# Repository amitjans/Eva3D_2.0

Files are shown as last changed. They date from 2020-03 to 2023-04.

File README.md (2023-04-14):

# Assembly Manual: Eva 4.0
<p align="center">
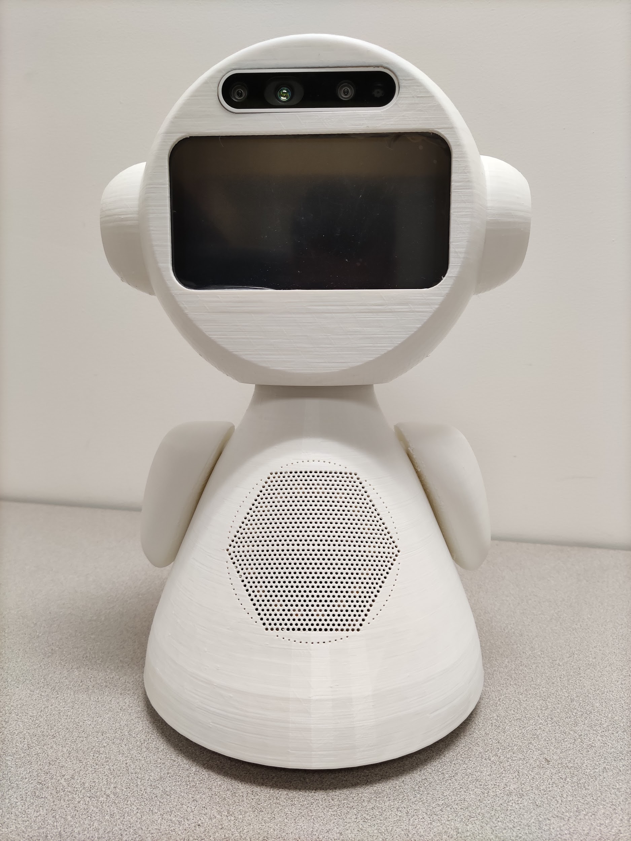
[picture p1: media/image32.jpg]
    
</p>

# Versions of the social robot Eva

Three versions of the social robot Eva were designed. The assembly demonstrated, as well as the images used in this manual, correspond to the most equipped version of the robot.

| Nombre | foto | Descripción |
| :--- | :---: | :--- |
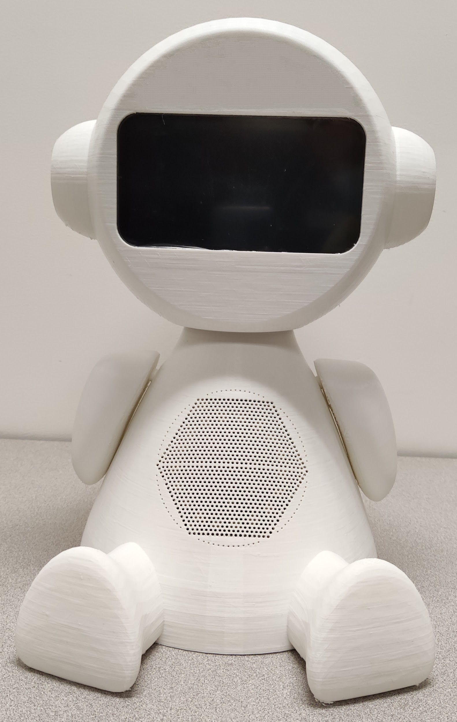
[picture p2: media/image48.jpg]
| Basic Eva |  | The basic version of the social robot Eva has three capabilities: <ul><li>Verbal interaction: through an array of microphones (Matrix Voice) and a speaker.</li><li>Eyes: through a 5.5” screen.</li><li>Head movement: through the use of two motors (Dynamixel AX-12A (Hard#10)).</li></ul> |
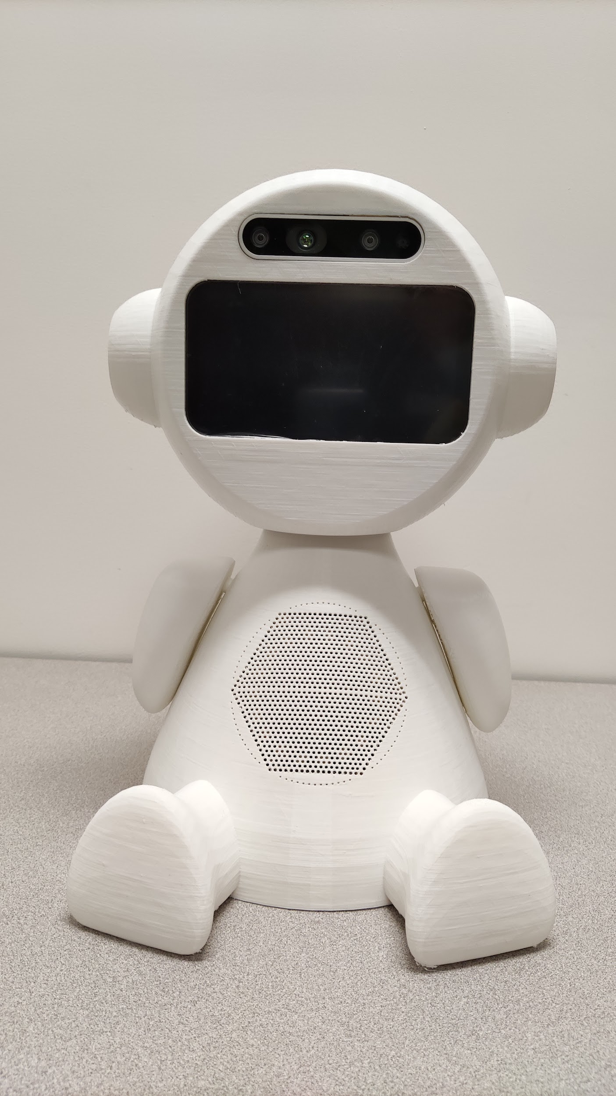
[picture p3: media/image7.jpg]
| Eva with camera |  | The camera version of the Eva social robot inherits the capabilities of the basic version. The new capabilities of this version are: <ul><li>Vision: using an Intel RealSense Depth Camera D435i (Hard#4).</li></ul> |
| Eva with camera and movement |  | The camera and movement version of the social robot Eva inherits the capabilities of the camera version. The new capabilities of this version include: <ul><li>Movement: using two new motors and wheels.</li></ul> |

# Basic Eva

<table border="0">
 <tr>
    <td>
        <ul>
            <li>Components
                <ul>
                    <li>Printables
                        <ul>
                            <li><a href="#Imp#1">Imp#1</a></li>
                            <li><a href="#Imp#3">Imp#3</a></li>
                            <li><a href="#Imp#5">Imp#5</a></li>
                            <li><a href="#Imp#7">Imp#7</a></li>
                            <li><a href="#Imp#9">Imp#9</a></li>
                            <li><a href="#Imp#10">Imp#10</a></li>
                            <li><a href="#Imp#11">Imp#11</a></li>
                            <li><a href="#Imp#12">Imp#12</a></li>
                            <li><a href="#Imp#13">Imp#13</a></li>
                            <li><a href="#Imp#14">Imp#14</a></li>
                        </ul>
                    </li>
                </ul>
                <ul>
                    <li>Electronics
                        <ul>
                            <li><a href="#Hard#1">Hard#1</a></li>
                            <li><a href="#Hard#2">Hard#2</a></li>
                            <li><a href="#Hard#17">Hard#17</a></li>
                            <li><a href="#Hard#8">Hard#8</a></li>
                            <li><a href="#Hard#10">Hard#10</a></li>
                            <li><a href="#Hard#11">Hard#11</a></li>
                            <li><a href="#Hard#13">Hard#13</a></li>
                            <li><a href="#Hard#14">Hard#14</a></li>
                            <li><a href="#Hard#15">Hard#15</a></li>
                        </ul>
                    </li>
                </ul>
            </li>
        </ul>
    </td>
    <td>
        <ul>
            <li>Assembly
                <ul>
                    <li><a href="#armando-el-cuello">Assembling the neck</a>
                        <ul>
                            <li><a href="#versión-estática">Static Version</a></li>
                            <li><a href="#raspberry-y-matrix-voice">Raspberry and Matrix Voice</a></li>
                        </ul>
                    </li>
                    <li><a href="#base-del-robot">Robot Base</a>
                        <ul>
                            <li><a href="#estático">Static</a></li>
                        </ul>
                    </li>
                    <li><a href="#ensamblaje-del-interior">Assembly of the interior</a></li>
                    <li><a href="#ensamblaje-de-la-cabeza">Assembly of the head</a>
                        <ul>
                            <li><a href="#sin-cámara">Without camera</a></li>
                            <li><a href="#pantalla">Display</a></li>
                        </ul>
                    </li>
                    <li><a href="#ensamblaje-final">Final assembly</a></li>
                </ul>
            </li>
        </ul>
    </td>
    <td></td>
 </tr>
</table>

# Eva with camera

<table border="0">
 <tr>
    <td>
        <ul>
            <li>Components
                <ul>
                    <li>Printables
                        <ul>
                            <li><a href="#Imp#2">Imp#2</a></li>
                            <li><a href="#Imp#3">Imp#3</a></li>
                            <li><a href="#Imp#4">Imp#4</a></li>
                            <li><a href="#Imp#5">Imp#5</a></li>
                            <li><a href="#Imp#7">Imp#7</a></li>
                            <li><a href="#Imp#9">Imp#9</a></li>
                            <li><a href="#Imp#10">Imp#10</a></li>
                            <li><a href="#Imp#11">Imp#11</a></li>
                            <li><a href="#Imp#12">Imp#12</a></li>
                            <li><a href="#Imp#13">Imp#13</a></li>
                            <li><a href="#Imp#14">Imp#14</a></li>
                        </ul>
                    </li>
                </ul>
                <ul>
                    <li>Electronics
                        <ul>
                            <li><a href="#Hard#1">Hard#1</a></li>
                            <li><a href="#Hard#2">Hard#2</a></li>
                            <li><a href="#Hard#17">Hard#17</a></li>
                            <li><a href="#Hard#4">Hard#4</a></li>
                            <li><a href="#Hard#8">Hard#8</a></li>
                            <li><a href="#Hard#10">Hard#10</a></li>
                            <li><a href="#Hard#11">Hard#11</a></li>
                            <li><a href="#Hard#13">Hard#13</a></li>
                            <li><a href="#Hard#14">Hard#14</a></li>
                            <li><a href="#Hard#15">Hard#15</a></li>
                        </ul>
                    </li>
                </ul>
            </li>
        </ul>
    </td>
    <td>
        <ul>
            <li>Assembly
                <ul>
                    <li><a href="#armando-el-cuello">Assembling the neck</a>
                        <ul>
                            <li><a href="#versión-estática">Static Version</a></li>
                            <li><a href="#raspberry-y-matrix-voice">Raspberry and Matrix Voice</a></li>
                        </ul>
                    </li>
                    <li><a href="#base-del-robot">Robot Base</a>
                        <ul>
                            <li><a href="#estático">Static</a></li>
                        </ul>
                    </li>
                    <li><a href="#ensamblaje-del-interior">Assembly of the interior</a></li>
                    <li><a href="#ensamblaje-de-la-cabeza">Assembly of the head</a>
                        <ul>
                            <li><a href="#con-cámara">With camera</a>
                                <ul>
                                    <li><a href="#cámara">Camera</a></li>
                                </ul>
                            </li>
                            <li><a href="#pantalla">Display</a></li>
                        </ul>
                    </li>
                    <li><a href="#ensamblaje-final">Final assembly</a></li>
                </ul>
            </li>
        </ul>
    </td>
    <td></td>
 </tr>
</table>

# Eva with camera and movement

<table border="0">
 <tr>
    <td>
        <ul>
            <li>Components
                <ul>
                    <li>Printables
                        <ul>
                            <li><a href="#Imp#2">Imp#2</a></li>
                            <li><a href="#Imp#3">Imp#3</a></li>
                            <li><a href="#Imp#6">Imp#4</a></li>
                            <li><a href="#Imp#8">Imp#5</a></li>
                            <li><a href="#Imp#9">Imp#7</a></li>
                            <li><a href="#Imp#10">Imp#9</a></li>
                            <li><a href="#Imp#11">Imp#10</a></li>
                            <li><a href="#Imp#12">Imp#11</a></li>
                            <li><a href="#Imp#13">Imp#12</a></li>
                            <li><a href="#Imp#14">Imp#13</a></li>
                        </ul>
                    </li>
                </ul>
                <ul>
                    <li>Electronics
                        <ul>
                            <li><a href="#Hard#1">Hard#1</a></li>
                            <li><a href="#Hard#2">Hard#2</a></li>
                            <li><a href="#Hard#3">Hard#3</a></li>
                            <li><a href="#Hard#4">Hard#4</a></li>
                            <li><a href="#Hard#5">Hard#5</a></li>
                            <li><a href="#Hard#6">Hard#6</a></li>
                            <li><a href="#Hard#7">Hard#7</a></li>
                            <li><a href="#Hard#8">Hard#8</a></li>
                            <li><a href="#Hard#9">Hard#9</a></li>
                            <li><a href="#Hard#10">Hard#10</a></li>
                            <li><a href="#Hard#11">Hard#11</a></li>
                            <li><a href="#Hard#12">Hard#12</a></li>
                            <li><a href="#Hard#13">Hard#13</a></li>
                            <li><a href="#Hard#14">Hard#14</a></li>
                            <li><a href="#Hard#15">Hard#15</a></li>
                        </ul>
                    </li>
                </ul>
            </li>
        </ul>
    </td>
    <td>
        <ul>
            <li>Assembly
                <ul>
                    <li><a href="#armando-el-cuello">Assembling the neck</a>
                        <ul>
                            <li><a href="#versión-móvil">Mobile Version</a></li>
                            <li><a href="#raspberry-y-matrix-voice">Raspberry and Matrix Voice</a></li>
                        </ul>
                    </li>
                    <li><a href="#base-del-robot">Robot Base</a>
                        <ul>
                            <li><a href="#móvil">Mobile</a></li>
                        </ul>
                    </li>
                    <li><a href="#ensamblaje-del-interior">Assembly of the interior</a></li>
                    <li><a href="#ensamblaje-de-la-cabeza">Assembly of the head</a>
                        <ul>
                            <li><a href="#con-cámara">With camera</a>
                                <ul>
                                    <li><a href="#cámara">Camera</a></li>
                                </ul>
                            </li>
                            <li><a href="#pantalla">Display</a></li>
                        </ul>
                    </li>
                    <li><a href="#ensamblaje-final">Final assembly</a></li>
                </ul>
            </li>
        </ul>
    </td>
    <td></td>
 </tr>
</table>

# Assembling the neck

To begin the assembly of the Eva robot, we will start with the interior, specifically the section that allows the head to move. For this, we will need the Dynamixel AX-12A (Hard#10) motors as well as the screws and parts included by the manufacturers along with these motors ([Hard#8](#Hard#8) and [#Hard#11](Hard#11)). The sequence of steps is shown below.

<table>
<tr>
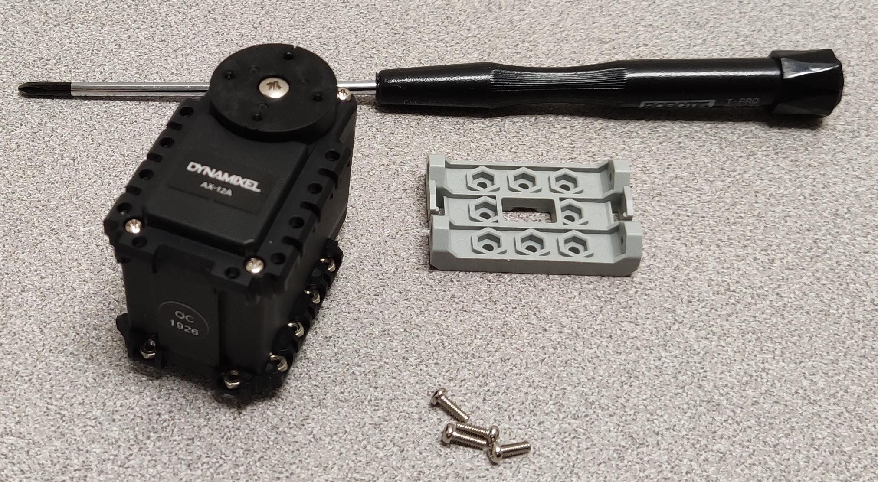
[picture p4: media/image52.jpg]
<td></td>
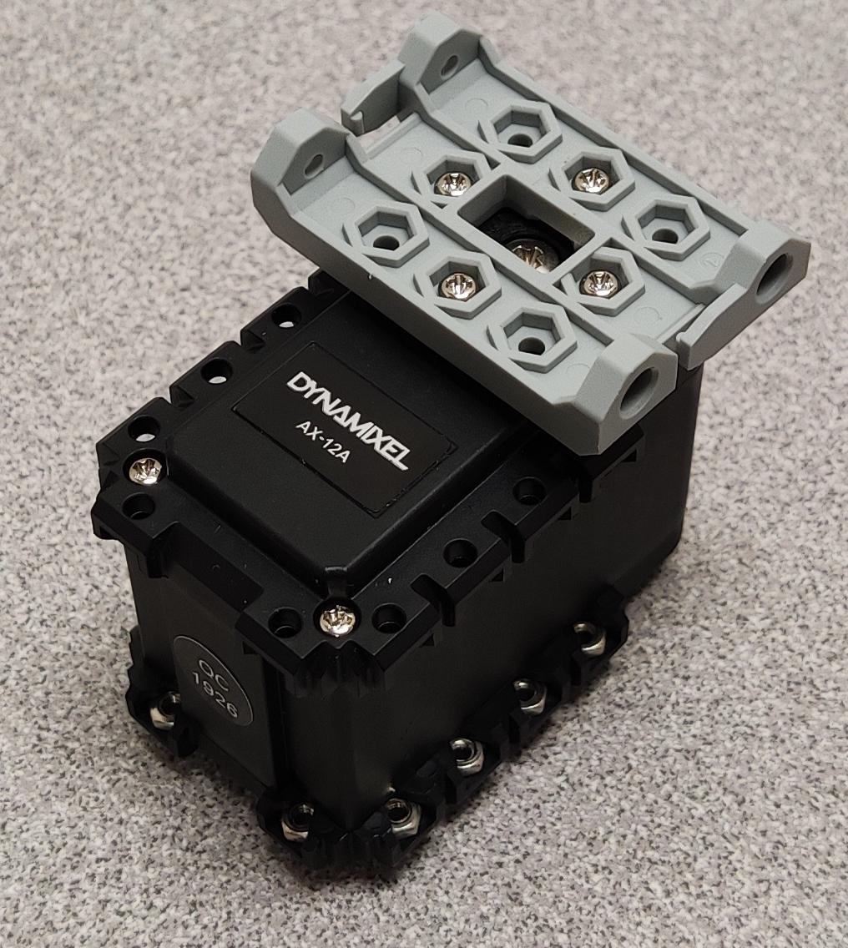
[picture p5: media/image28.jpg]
<td></td>
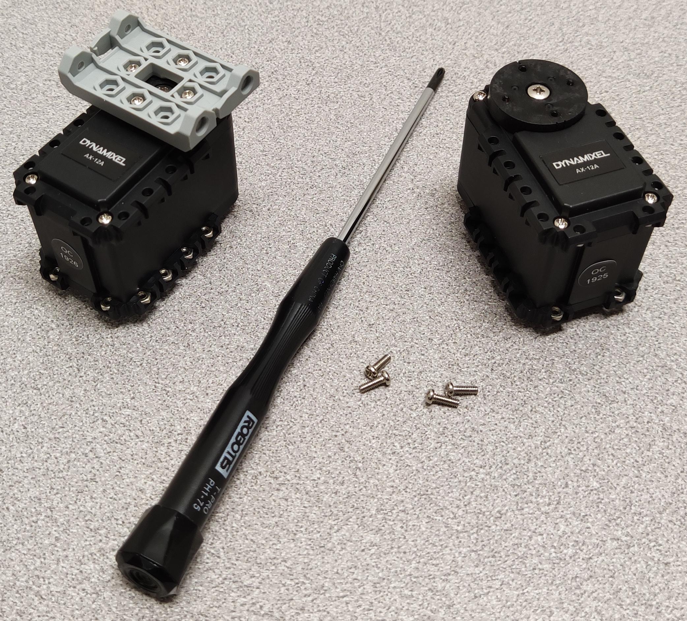
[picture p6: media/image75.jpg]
<td></td>
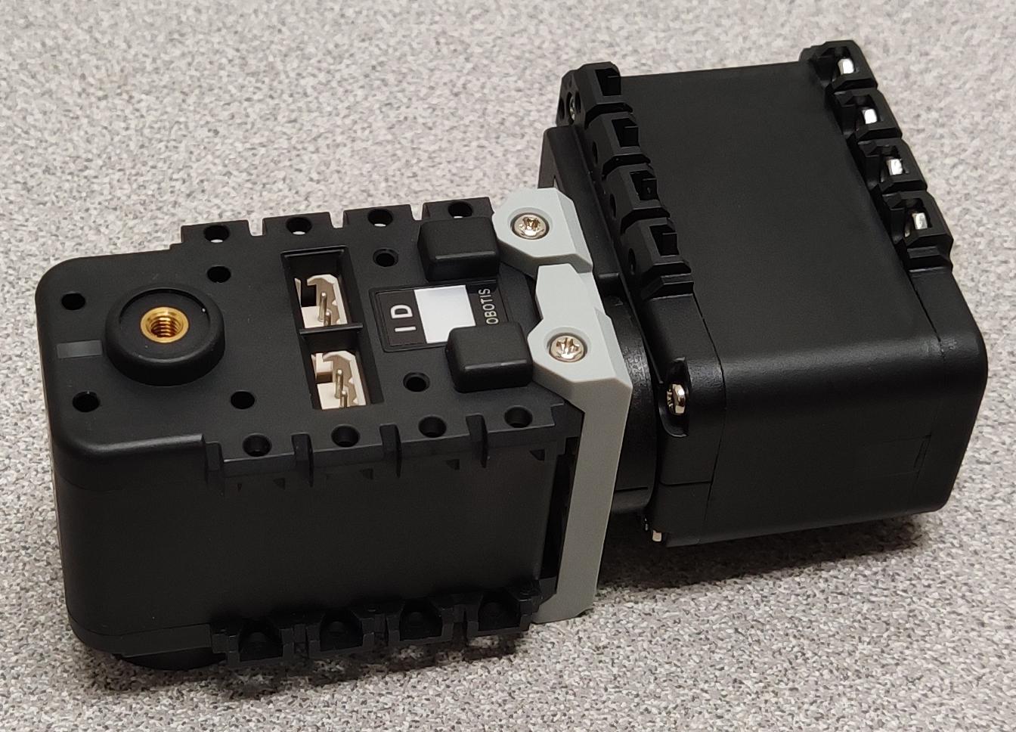
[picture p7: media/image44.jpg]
<td></td>
</tr>
<tr>
<td colspan="2">Attach the base motor (Hard#10) to the Bioloid Frame F3 (Hard#11).</td>
<td colspan="2">Attach the second motor (Hard#10) to the first using the Bioloid Frame F3 (Hard#11).</td>
</tr>
<tr>
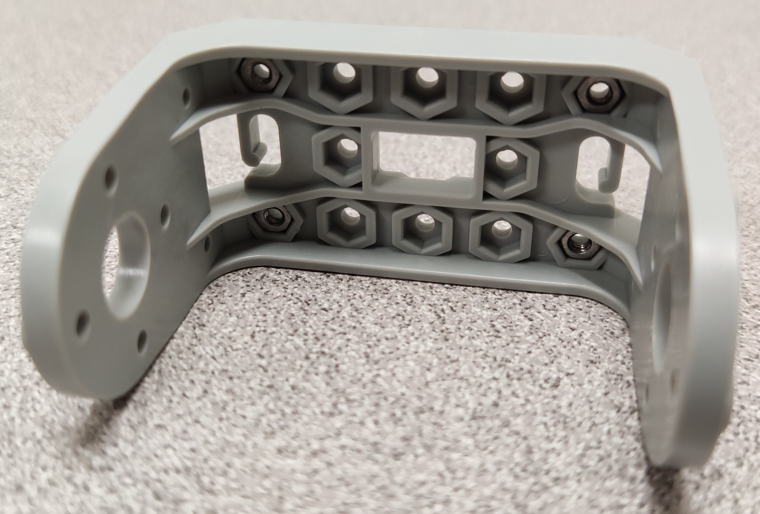
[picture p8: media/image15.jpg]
<td colspan="2"></td>
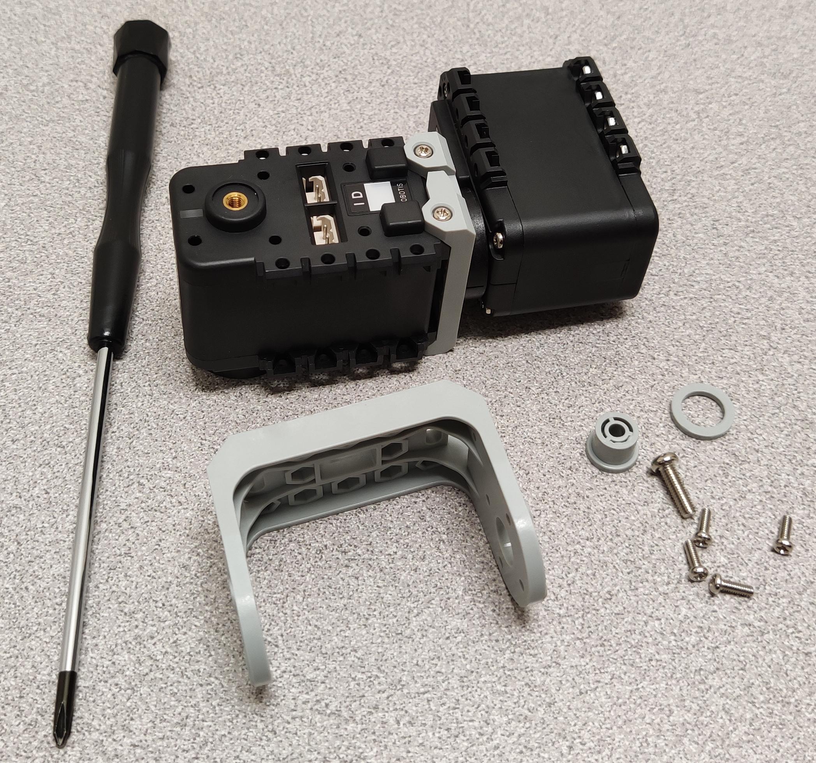
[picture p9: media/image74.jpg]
<td></td>
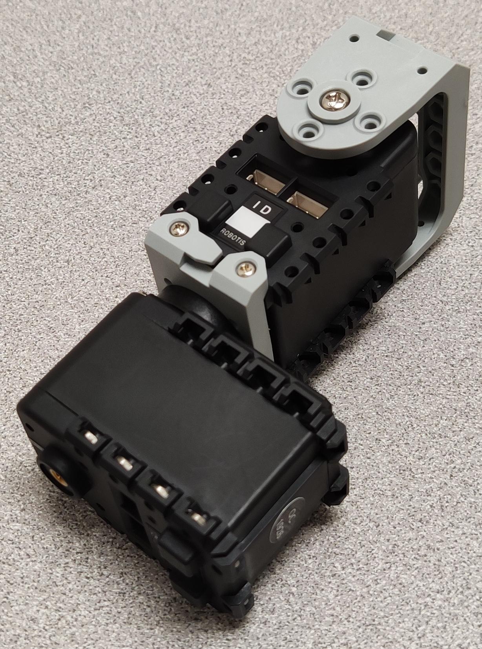
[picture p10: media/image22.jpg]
<td></td>
</tr>
<tr>
<td colspan="2">Place M2 nuts on the head support, Bioloid Frame F2 (Hard#8).</td>
<td colspan="2">Attach the head support, Bioloid Frame F2 (Hard#8) to the second motor (Hard#10).</td>
</tr>
</table>

Once both motors are attached, the first one will be screwed onto the "Motor Base". For this, we will use the screws provided by the seller. The nuts will be fixed to the motor and the screws will come from the opposite side of the motors.

<table>
<tr>
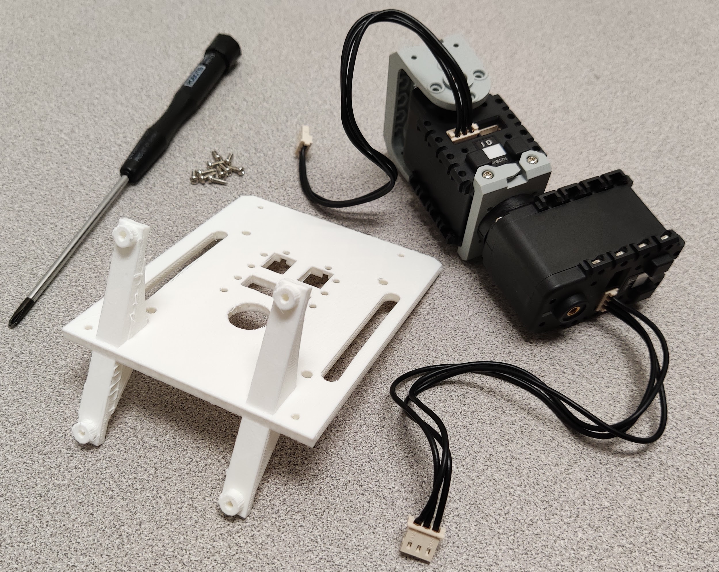
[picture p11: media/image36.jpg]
<td></td>
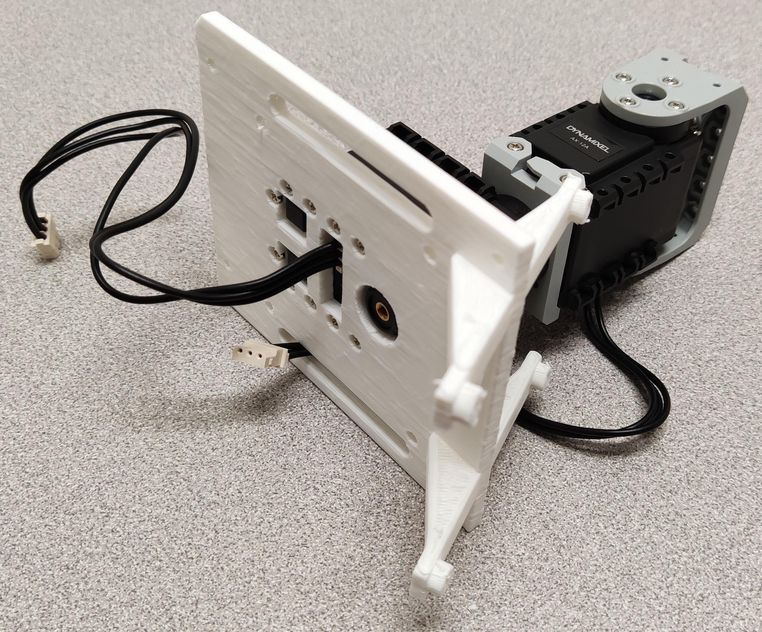
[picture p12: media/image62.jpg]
<td></td>
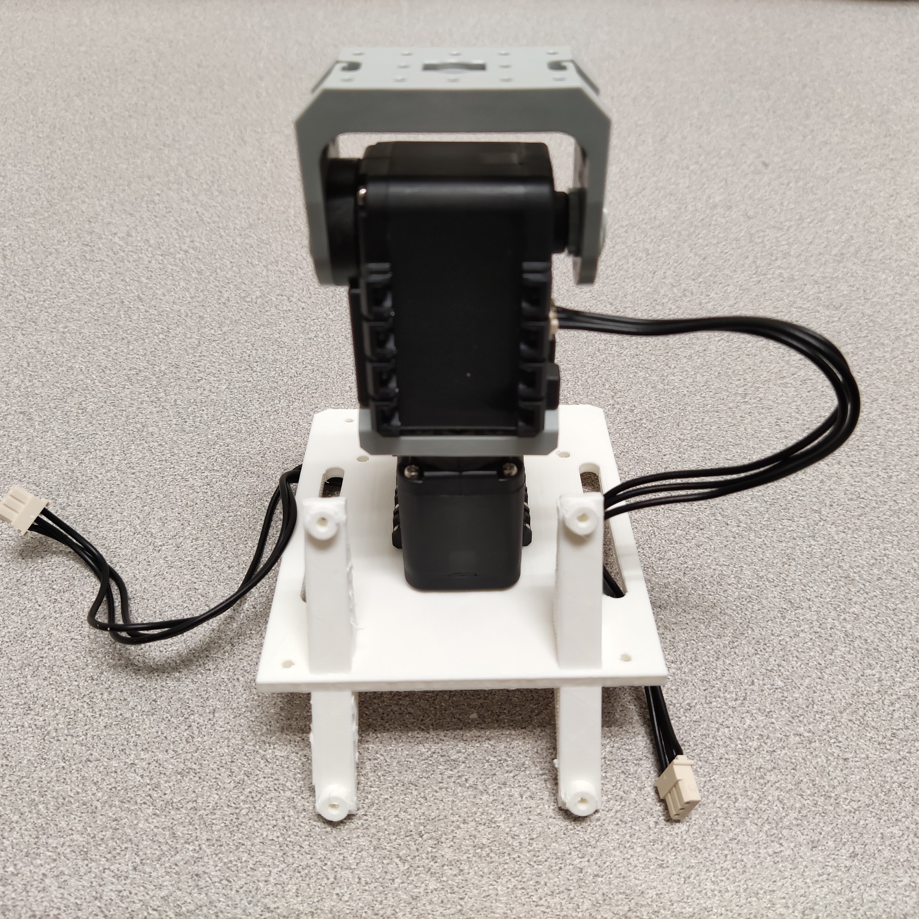
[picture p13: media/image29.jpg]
<td></td>
</tr>
<tr>
<td colspan="3">Fix the motor assembly (Hard#10) to the Motor Base (Imp#9)</td>
</tr>
</table>

**Note:** Before continuing with the next step, it is recommended to connect the cables that will communicate the motors with the control board to the motors.

## Static version 

Next, we will attach the control board responsible for the motors to the "Motor Base" (Imp#9Imp#9). In this case, we have chosen the "ArbotiX-M" (Hard#17Hard#17) control board. We will use four "PCB Mounts" (Imp#15Imp#15) to attach the board to the "Motor Base" (Imp#9Imp#9), using M3x8 screws for both.

## Mobile version

Afterwards, we will attach the motor control board, in this case, the OpenCR 1.0 (Hard#3), to the “base for motors” (Imp#9) using four "PCB Mounts" (Imp#14). The mounts will be screwed into the “base for motors” (Imp#9) and the controller board will be attached to these mounts using M2.5x8 screws and M2.5 nuts.

<table>
<tr>
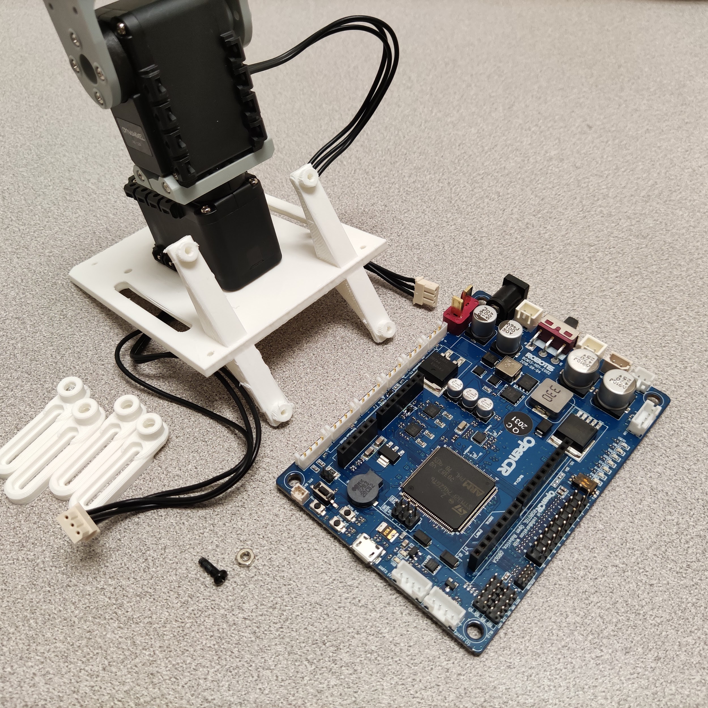
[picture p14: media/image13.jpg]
<td colspan="2"></td>
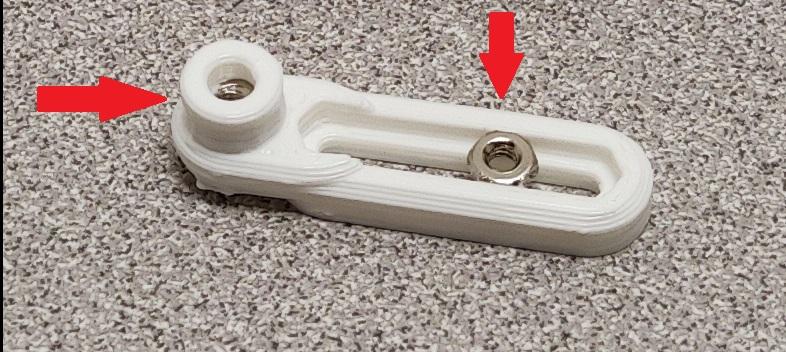
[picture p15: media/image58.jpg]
<td colspan="2"></td>
</tr>
<tr>
<td colspan="4">Next, we will mount the OpenCR 1.0 board (Hard#3) onto the motor base (Imp#9) using four PCB supports (Imp#14). To do this, we will initially place 2 M2.5 nuts on each PCB support (Imp#14) as shown in the image above.</td>
</tr>
<tr>
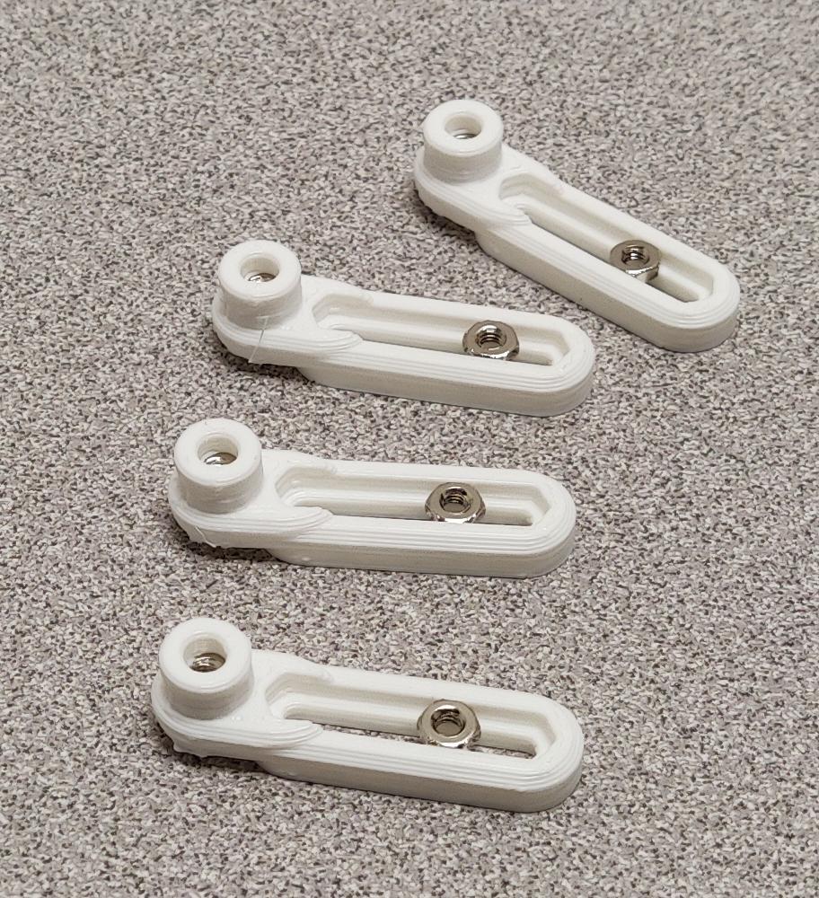
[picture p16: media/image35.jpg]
<td></td>
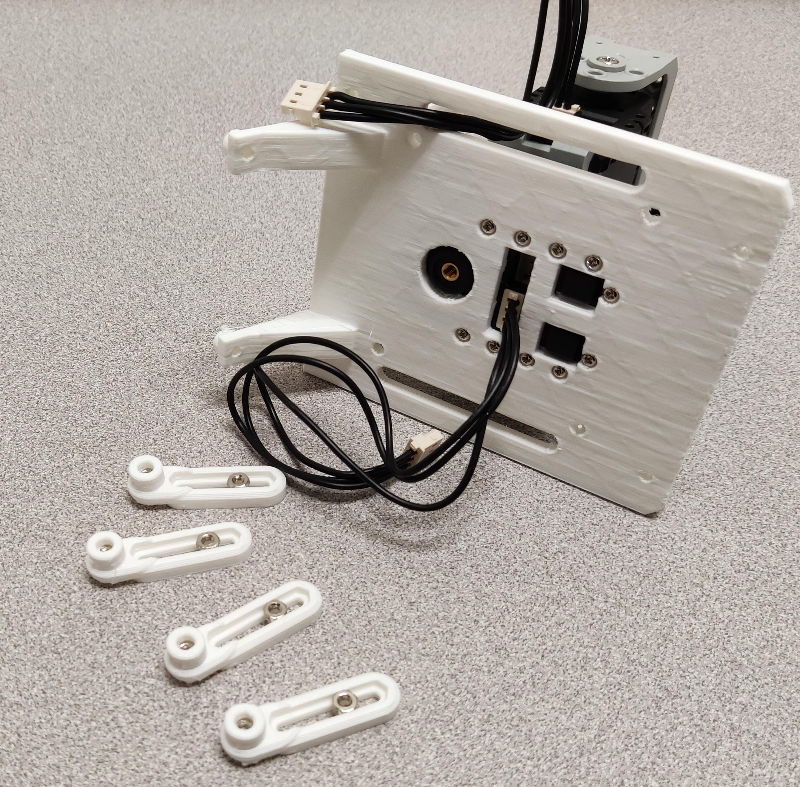
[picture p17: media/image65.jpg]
<td></td>
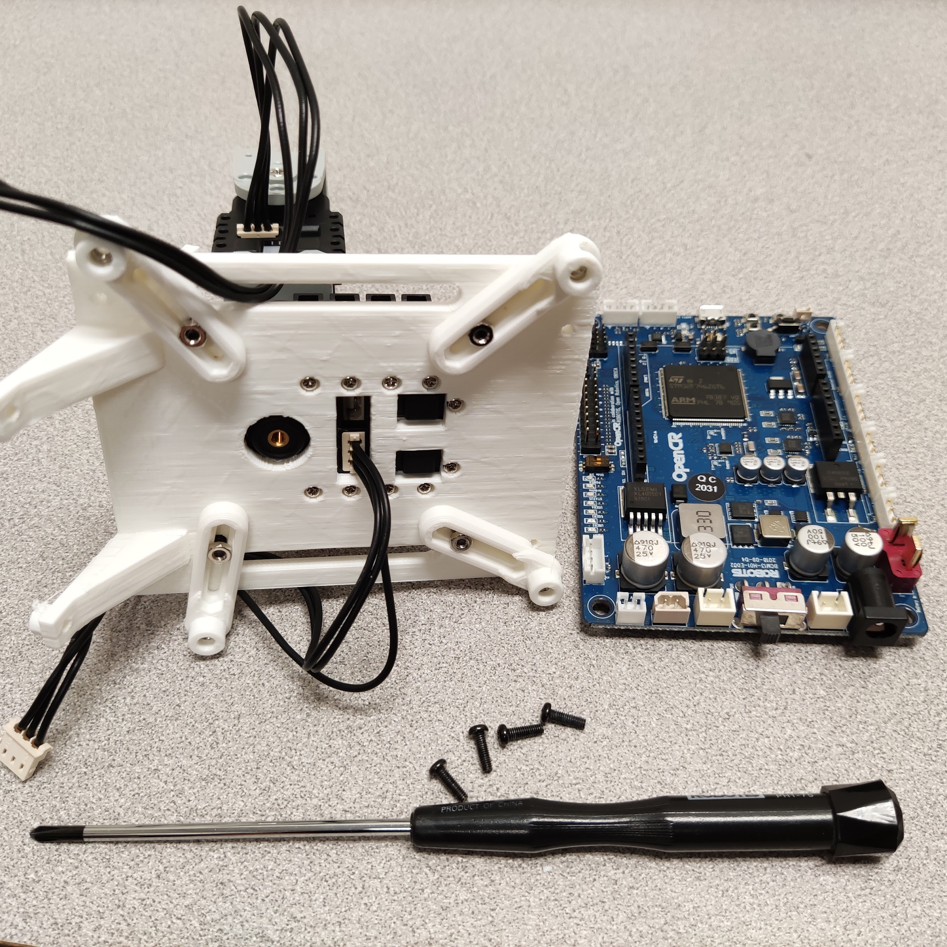
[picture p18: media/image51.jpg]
<td></td>
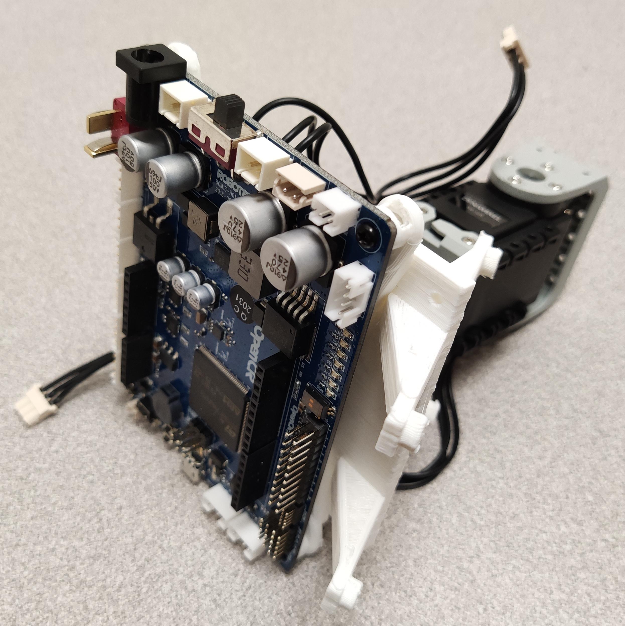
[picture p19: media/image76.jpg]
<td></td>
</tr>
<tr>
<td colspan="4">Finally, we screw the PCB supports (Imp#14) and the OpenCR 1.0 board (Hard#3) to them onto the motor base (Imp#9).</td>
</tr>
</table>

## Raspberry and Matrix Voice

Once the previous step is completed, the Raspberry Pi (Hard#13) and the Matrix Voice (Hard#14) can be placed in their positions. The Raspberry Pi (Hard#13) will be secured to the base using four M2.5x12 screws.

<table>
<tr>
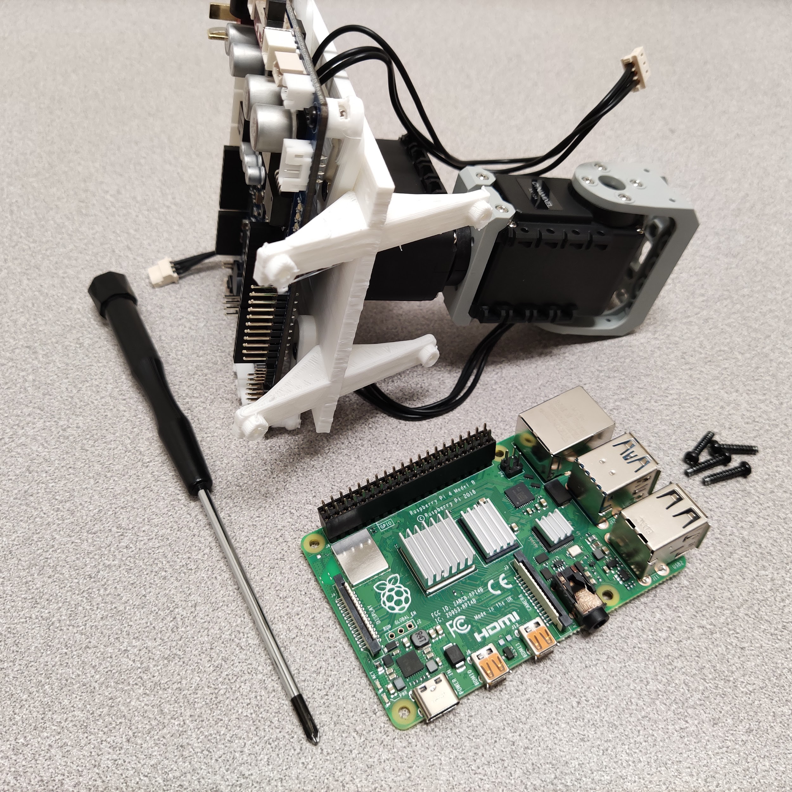
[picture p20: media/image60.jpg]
<td></td>
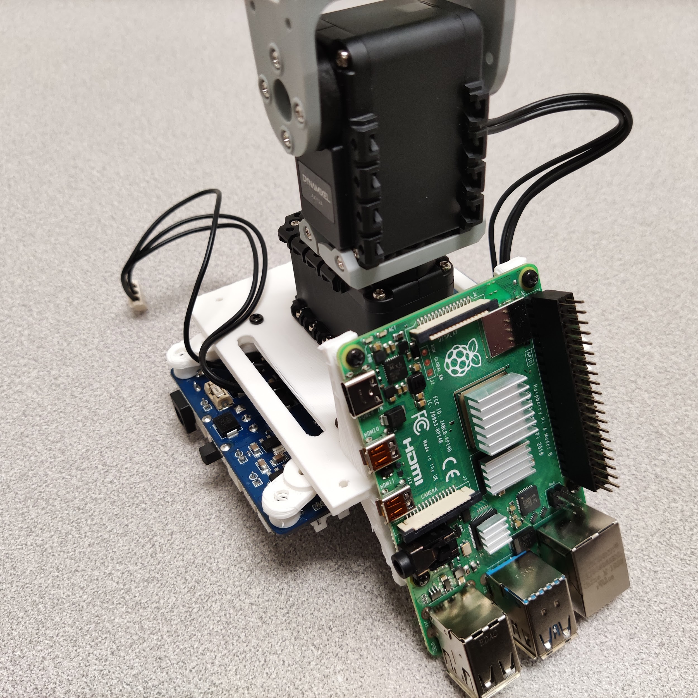
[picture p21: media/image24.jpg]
<td></td>
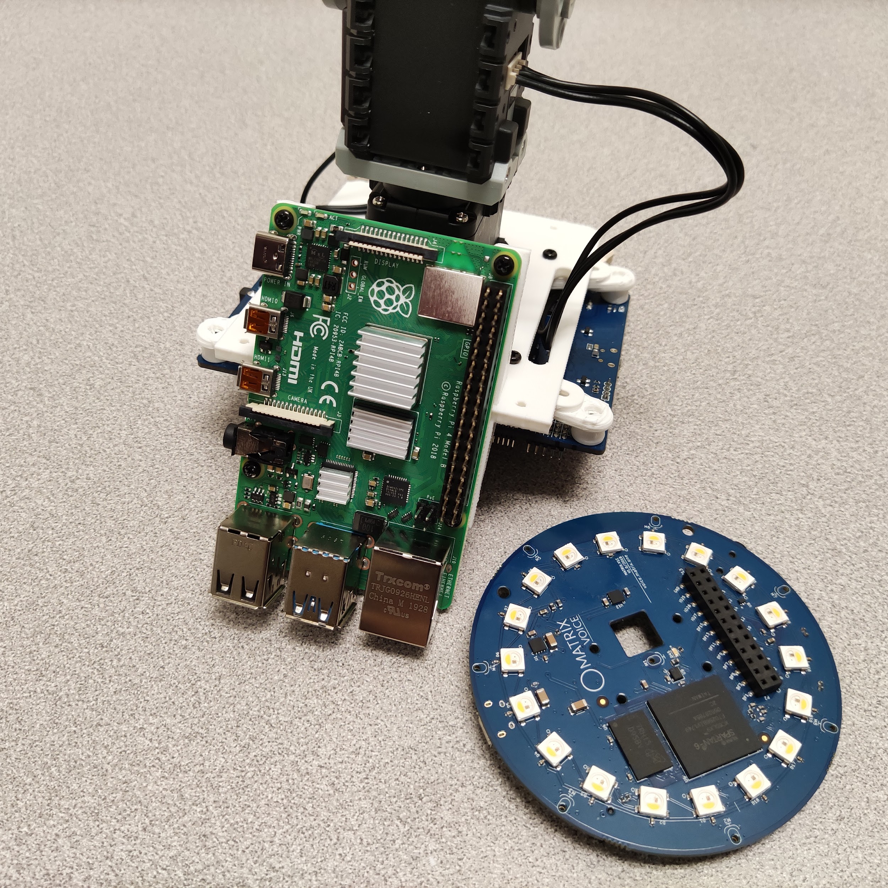
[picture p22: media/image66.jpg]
<td></td>
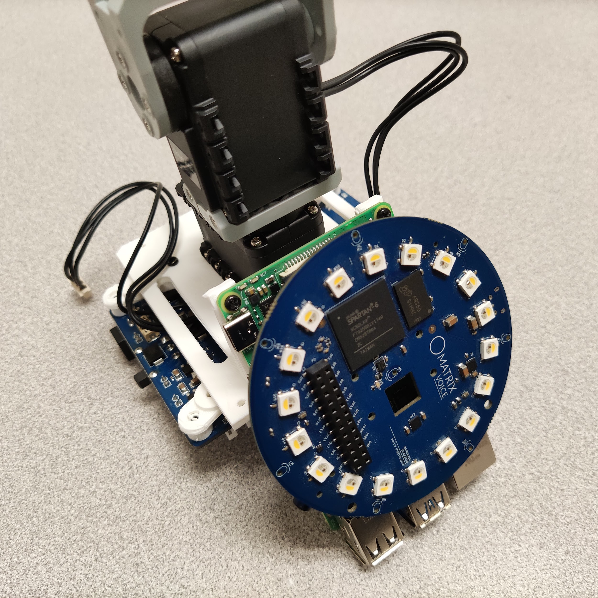
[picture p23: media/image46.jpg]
<td></td>
</tr>
<tr>
<td colspan="2">Placing the Raspberry Pi (Hard#13) on the motor base (Imp#9).</td>
<td colspan="2">Placing the Matrix Voice (Hard#14) on top of the Raspberry Pi (Hard#13) using a GPIO Stacking Header (Hard#15).</td>
</tr>
</table>

# Base of the Robot

The assembly of the robot base will depend on the version of the robot being assembled: static or mobile.

## Static

For the static version of the robot, we will use the Base (Imp#7) to which we will attach the battery (LI-PO 11.1V 1800mAh Lb-12 19.98Wh 5C) (Hard#5) with the structures that protrude from the center of the base.

## Mobile

For this step, we will need two XL430-W250-T motors (Hard#9), two wheels (Hard#6), and two tires (Hard#7), a lithium battery - for this case, the "LI-PO 11.1V 1800mAh Lb-12c 19.98Wh 5C" (Hard#5) was used, a ball caster (Hard#12), and the "Mobile Base" (Imp#8) to which everything will be attached.

First, the tires (Hard#7) will be placed on the wheels (Hard#6), and then the wheels will be screwed onto the motors (Hard#9) using four M2x4 screws for each one.

<table>
<tr>
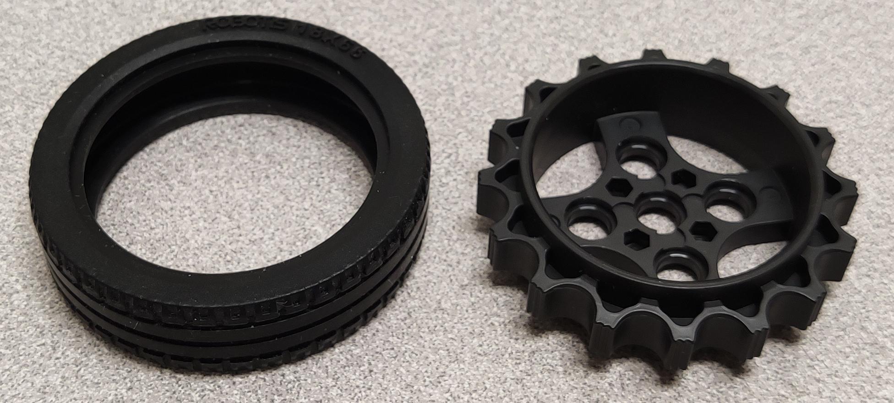
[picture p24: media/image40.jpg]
<td></td>
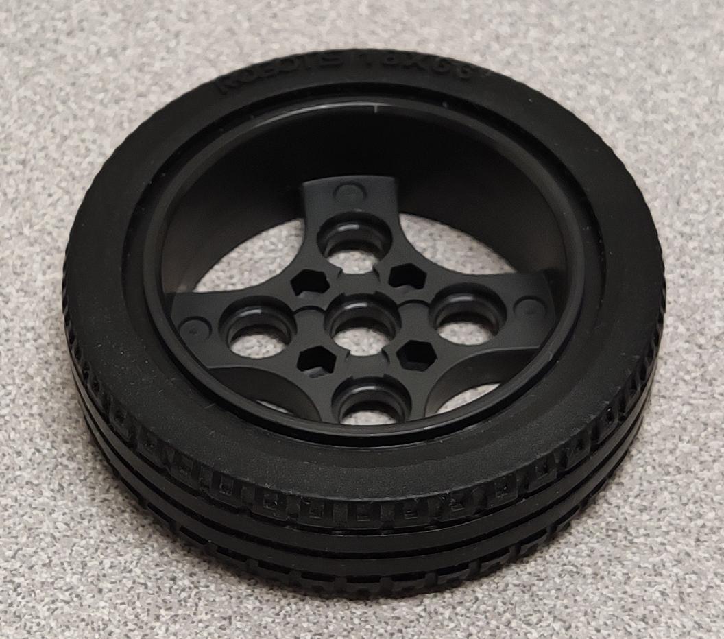
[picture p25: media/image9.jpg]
<td></td>
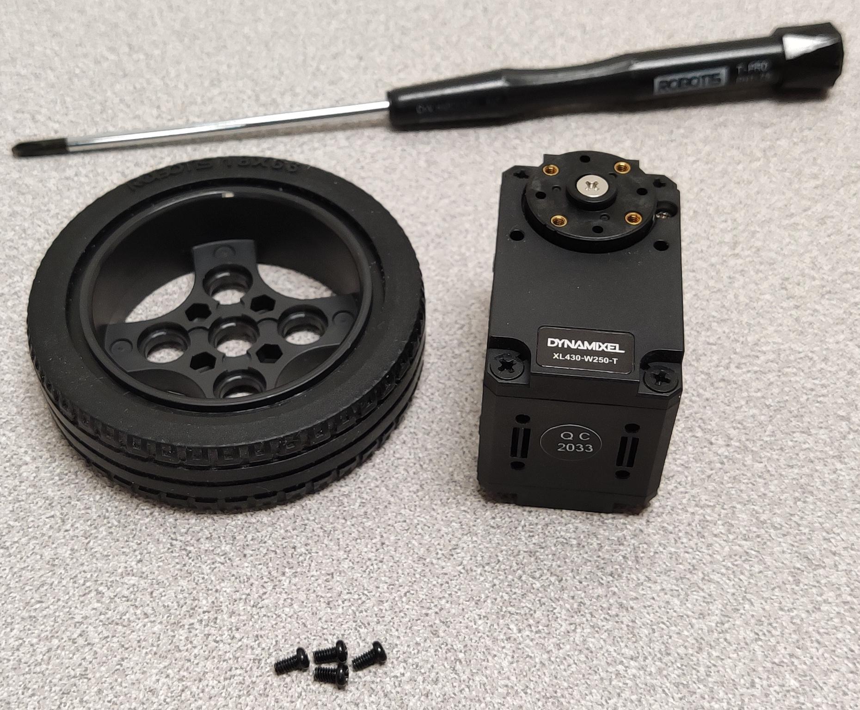
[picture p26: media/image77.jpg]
<td></td>
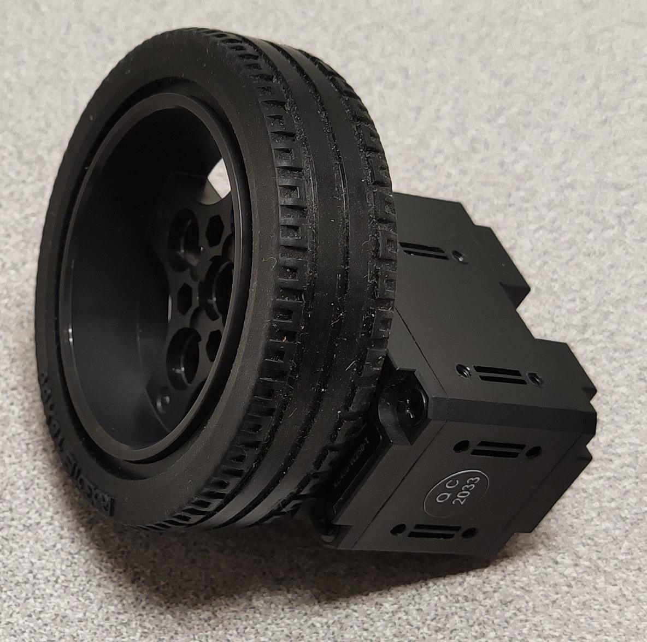
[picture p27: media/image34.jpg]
<td></td>
</tr>
<tr>
<td colspan="4">Assembling the wheels: The tires (Hard#7) will be placed on the wheels (Hard#6) and the latter will be fixed to the motors (Hard#9).</td>
</tr>
</table>

The motors (Hard#9) will be screwed onto the base using four M2.5x12 screws, and for the "Ball Caster" (Hard#12) four M2x6 screws will be used.

<table>
<tr>
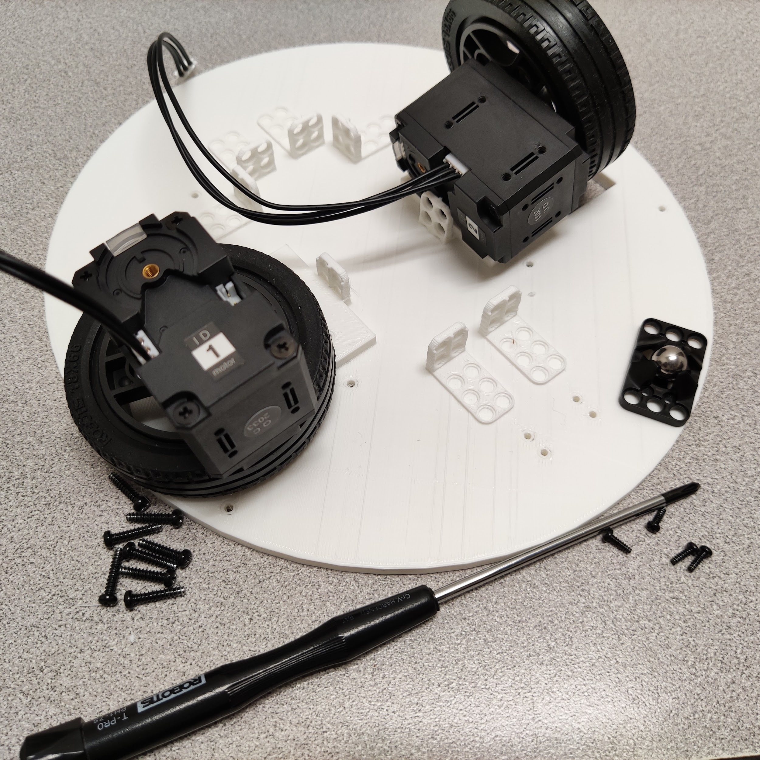
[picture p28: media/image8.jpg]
<td></td>
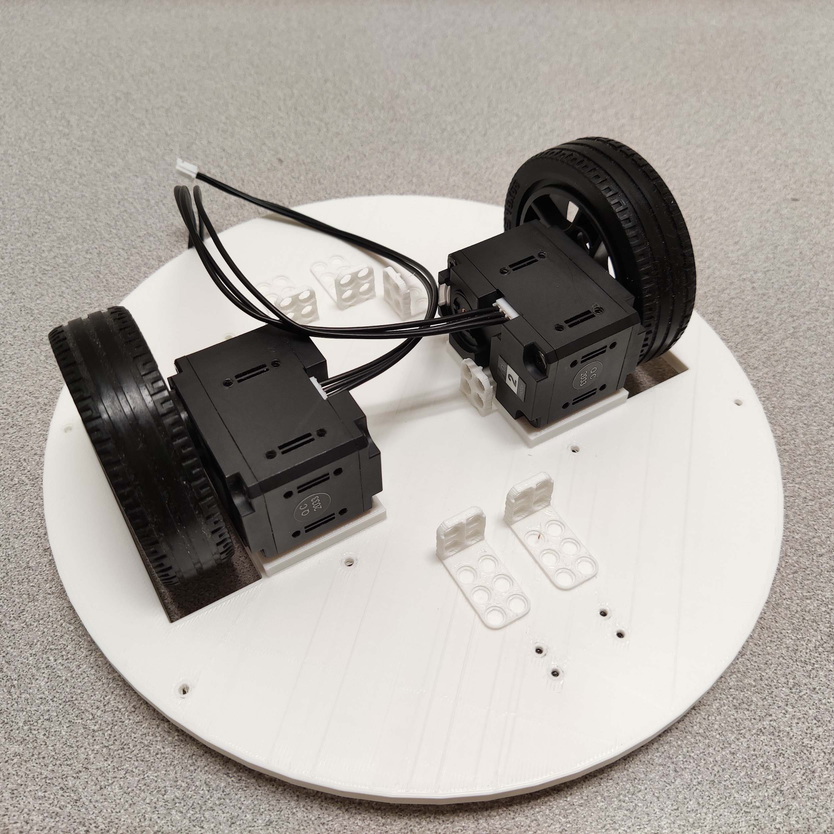
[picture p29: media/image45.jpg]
<td></td>
</tr>
<tr>
<td colspan="2">Assembling the wheels: The tires (Hard#7) will be placed on the wheels (Hard#6) and the latter will be fixed to the motors (Hard#9).</td>
</tr>
</table>

Attaching the previously assembled wheels to the base (Imp#8).

The battery will be attached with the structures that protrude from the center of the base.

# Assembly of the interior

Once the previous two steps are completed, the resulting parts will be joined using four plate supports (Imp#10), for which eight M3x8 screws will be used.

<table>
<tr>
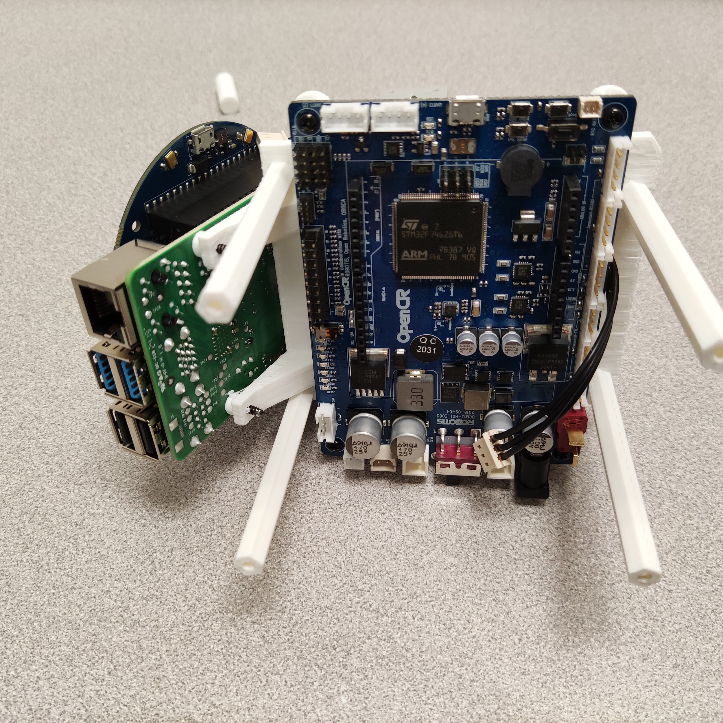
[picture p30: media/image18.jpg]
<td></td>
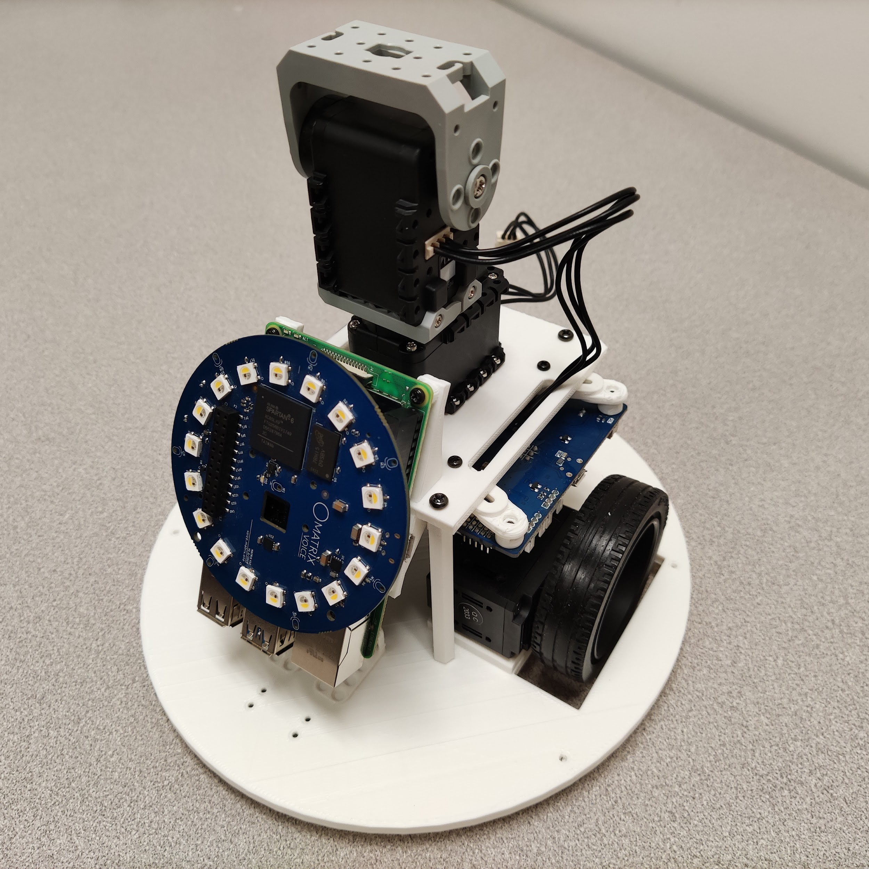
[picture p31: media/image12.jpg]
<td></td>
</tr>
</table>

**Note**: For this case, the shown images correspond to the mobile version of the robot.

**Note**: In the case of the mobile version, it is recommended to connect the motors before joining both parts.

# Assembly of the head

The assembly of the robot's head will depend on the version of the robot being assembled: with camera or without camera.

**Note**: In both cases, this step will vary if a rotating or 90-degree HDMI tip cable is used instead of an adapter, in which case the size of the connector and its orientation must be taken into account.

**Note**: The hole left in the base of the head is intended to allow the cables to pass through. In the assembly carried out, it is taken into account that the HDMI cable, a MicroUSB to USB-A cable (related to the touch functionality of the screen), and the speaker power cable will pass through this space if needed.

## With camera

For this case, we will use the printable parts Head with camera (Imp#2), Back cover of the head (Imp#3), Support for the screen (Imp#13), and Camera spacers (Imp#4), 5.5" screen with a 16:9 aspect ratio (Hard#1), Rotatable male-female HDMI adapter (Hard#2), Intel RealSense Depth Camera D435i (Hard#4), and a Speaker (Hard#16).

### Camera

For this case, the first step will be to place the camera (Hard#4), which will be screwed onto the support designed for it, using two M3x10 screws and two spacers (Imp#4).

<table>
<tr>
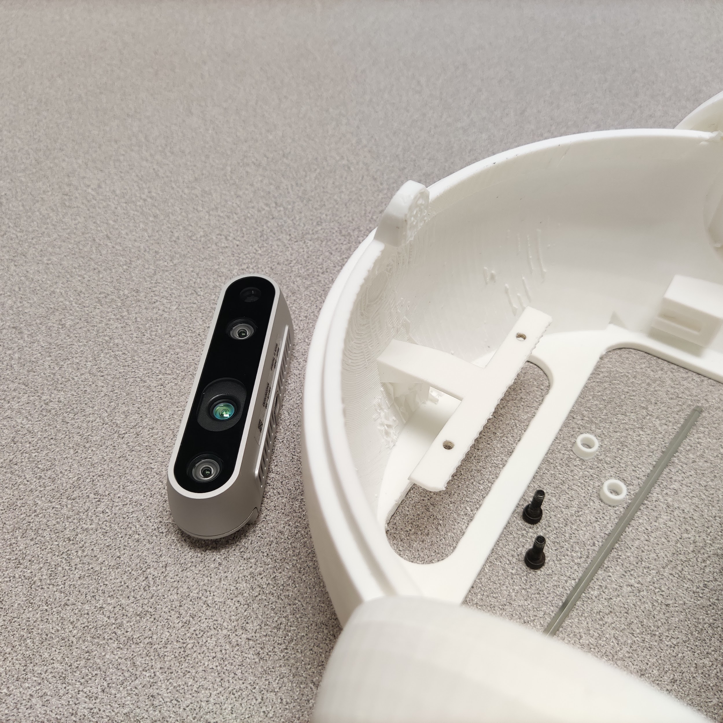
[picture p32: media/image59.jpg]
<td></td>
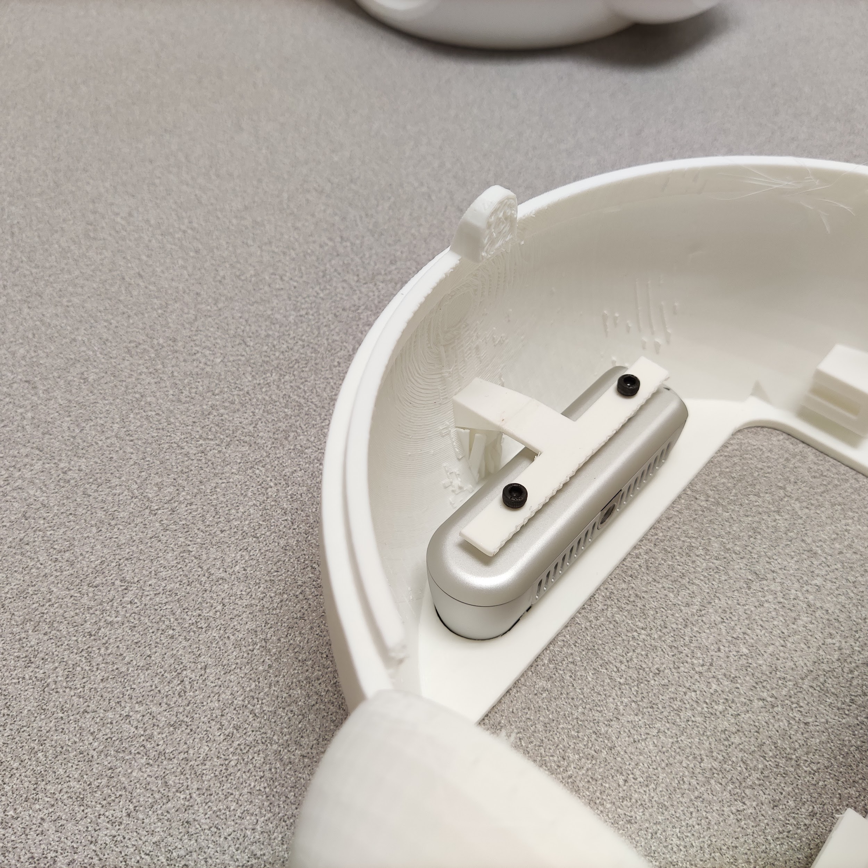
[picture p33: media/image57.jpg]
<td></td>
</tr>
</table>

Next, we will continue with the steps described in the [Screen]() section.

## Without camera

For this case, we will use the printable parts Head (Imp#1), Back cover for the head (Imp#3), and Support for the screen (Imp#13), in addition to a 5.5" screen with a 16:9 aspect ratio (Hard#1), a rotating male-female HDMI adapter (Hard#2), and a Speaker (Hard#16).

## Display

Initially, the screen (Hard#1) will be placed, which is recommended to be connected with the HDMI adapter (Hard#2) and the speaker cable, for greater ease.

<table>
<tr>
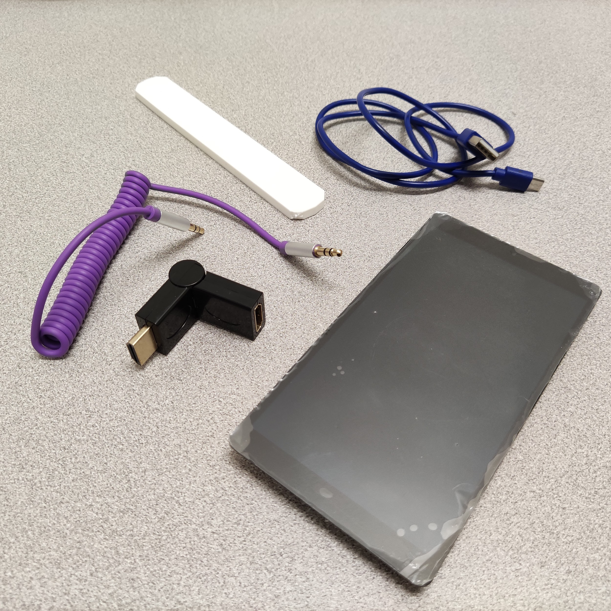
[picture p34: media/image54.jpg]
<td></td>
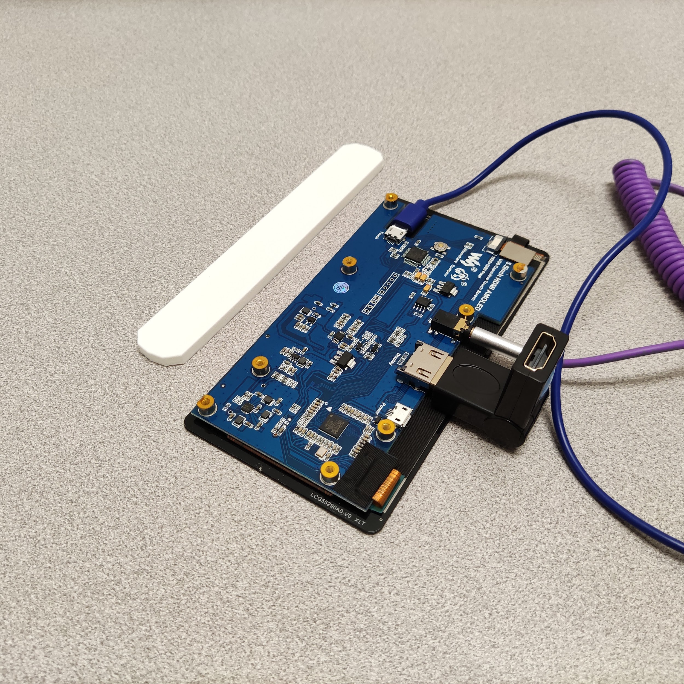
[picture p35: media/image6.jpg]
<td></td>
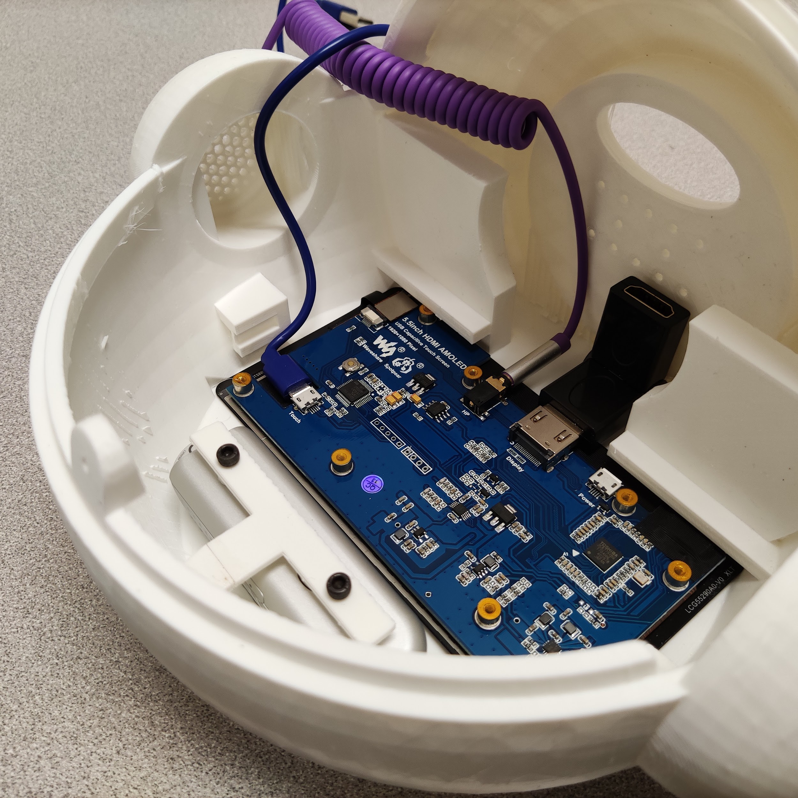
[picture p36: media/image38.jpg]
<td></td>
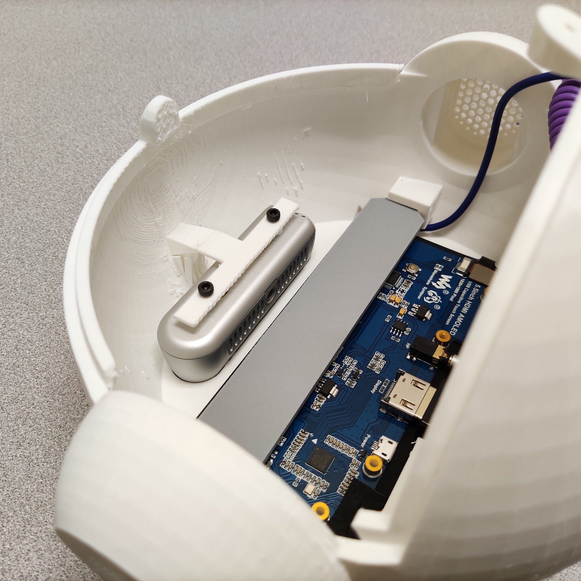
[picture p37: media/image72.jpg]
<td></td>
</tr>
<tr>
<td colspan="2">We connect the cables and the adapter (Hard#2) to the screen (Hard#1).</td>
<td colspan="2">We place the screen (Hard#1) on the head (Imp#1) and fix it with the screen holder (Imp#13).</td>
</tr>
<tr>
    <td colspan="4">
        <p align="center">
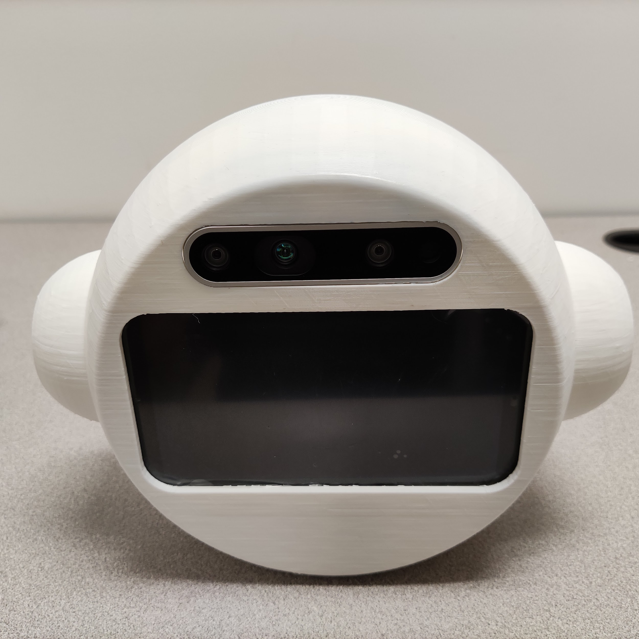
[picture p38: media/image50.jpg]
            </td>
        </p>
    </td>
</tr>
</table>

# Final assembly

To complete the assembly of the robot, we will attach the interior assembly to the body of the robot using four M3x8 screws.

**Note:** There are two versions of the robot body, Static Body (Imp#5) and Mobile Body (Imp#6). The difference between these is the presence/absence of legs. For the mobile version, we will use the version without legs. This choice is a design decision made by our team, as there is no physical element that prevents the use of either variant of the body.

Next, we will attach the Arms (Imp#11) to the body using an Arm Bracket (Imp#12) for each arm.

<p align="center">
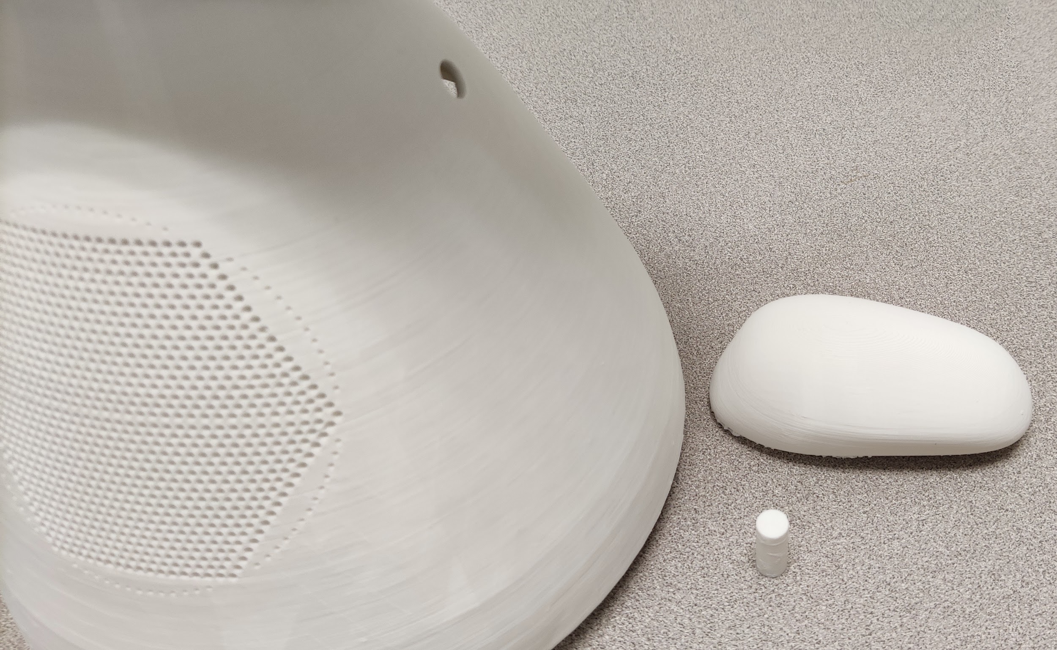
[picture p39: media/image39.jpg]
    
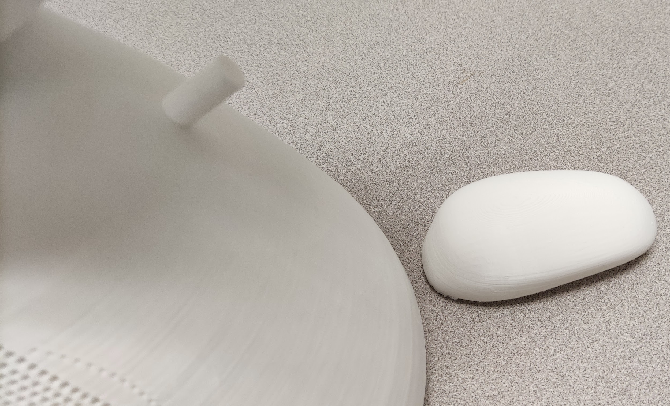
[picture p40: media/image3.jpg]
    
    
</p>

We will place the body (Imp#5 or Imp#6) onto the base (Imp#7 or Imp#8) using four M3x8 screws, so that the body covers the interior and the Matrix Voice is aligned with the body's grille.
Once this step is completed, we will attach the head (Imp#1 or Imp#2), which is screwed onto the neck's "Bioloid Frame F2" (Hard#8), for which we previously placed four nuts.
<p align="center">
    
</p>

For this assembly, a Philips Bluetooth speaker (Hard#16Hard#16) was used, which was fixed to the Head Cover (Imp#3Imp#3) using zip ties.
<p align="center">
    
    
</p>

Finally, we connect the speaker and place the Head Cover (Imp#3Imp#3), which we fix to the head using an M1x8 screw.
<p align="center">
    
    
</p>

Once this step is completed, the robot will look as follows according to the assembled version.

<p align="center">
    
    
    
</p>

# Appendix 1: List of parts

| Nombre | Foto | Descripción |
| :--- | :---: | :--- |
| <span id="Hard#1">Hard#1</span> |  | Waveshare 5.5\" HDMI AMOLED |
| <span id="Hard#2">Hard#2</span> |  | Adaptador HDMI macho-hembra giratorio |
| <span id="Hard#3">Hard#3</span> |  | OpenCR 1.0 |
| <span id="Hard#4">Hard#4</span> |  | Intel® RealSense™ Depth Camera D435i |
| <span id="Hard#5">Hard#5</span> |  | LI-PO 11.1V 1800mAh Lb-12 19.98Wh 5C |
| <span id="Hard#6">Hard#6</span> |  | Rueda x 2 |
| <span id="Hard#7">Hard#7</span> |  | Neumático x 2 |
| <span id="Hard#8">Hard#8</span> |  | Bioloid Frame F2 |
| <span id="Hard#9">Hard#9</span> |  | Dynamixel XL430-W250-T |
| <span id="Hard#10">Hard#10</span> |  | Dynamixel AX-12A |
| <span id="Hard#11">Hard#11</span> |  | Bioloid Frame F3 |
| <span id="Hard#12">Hard#12</span> |  | Ball Caster |
| <span id="Hard#13">Hard#13</span> |  | Raspberry Pi 4 |
| <span id="Hard#14">Hard#14</span> |  | Matrix Voice |
| <span id="Hard#15">Hard#15</span> |  | Cabezal de apilado GPIO |
| <span id="Hard#16">Hard#16</span> |  | Bocina Philips |
| <span id="Hard#17">Hard#17</span> |  | ArbotiX-M |

# Appendix 2: List of printable parts

| Modelo | Nombre | Descarga |
| :--- | :---: | :--- |
| <span id="Imp#1">Imp#1</span> |  | [Cabeza](https://github.com/amitjans/Eva3D_2.0/blob/master/stl/v4/Kit%20basico/cabeza.stl) |
| <span id="Imp#2">Imp#2</span> |  | [Cabeza con cámara](https://github.com/amitjans/Eva3D_2.0/blob/master/stl/v4/Kit%20basico%20%2B%20modulo%20camara/cabeza.stl) |
| <span id="Imp#3">Imp#3</span> |  | [Tapa cabeza](https://github.com/amitjans/Eva3D_2.0/blob/master/stl/v4/Piezas%20generales/tapa_cabeza.stl) |
| <span id="Imp#4">Imp#4</span> |  | [Separadores para la Cámara](https://github.com/amitjans/Eva3D_2.0/blob/master/stl/v4/Kit%20basico%20%2B%20modulo%20camara/separador.stl) 
| <span id="Imp#5">Imp#5</span> |  | [Cuerpo estático](https://github.com/amitjans/Eva3D_2.0/blob/master/stl/v4/Kit%20basico/cuerpo.stl) |  
| <span id="Imp#6">Imp#6</span> |  | [Cuerpo móvil](https://github.com/amitjans/Eva3D_2.0/blob/master/stl/v4/Kit%20base%20movil/cuerpo_movil.stl) 
| <span id="Imp#7">Imp#7</span> |  | [Base](https://github.com/amitjans/Eva3D_2.0/blob/master/stl/v4/Kit%20basico/base.stl) | 
| <span id="Imp#8">Imp#8</span> |  | [Base móvil](https://github.com/amitjans/Eva3D_2.0/blob/master/stl/v4/Kit%20base%20movil/base_movil_1.stl) |
| <span id="Imp#9">Imp#9</span> |  | [Base de Motores](https://github.com/amitjans/Eva3D_2.0/blob/master/stl/v4/Kit%20basico/base_2.stl) |
| <span id="Imp#10">Imp#10</span> |  | [Soportes de la Base de Motores x 4](https://github.com/amitjans/Eva3D_2.0/blob/master/stl/v4/Piezas%20generales/soportes.stl) |
| <span id="Imp#11">Imp#11</span> |  | [Brazo x 2](https://github.com/amitjans/Eva3D_2.0/blob/master/stl/v4/Piezas%20generales/brazo.stl) |
| <span id="Imp#12">Imp#12</span> |  | [Soporte para brazos x 2](https://github.com/amitjans/Eva3D_2.0/blob/master/stl/v4/Piezas%20generales/union_brazo.stl) |
| <span id="Imp#13">Imp#13</span> |  | [Soporte para la pantalla](https://github.com/amitjans/Eva3D_2.0/blob/master/stl/v4/Piezas%20generales/soporte_pantalla.stl) |
| <span id="Imp#14">Imp#14</span> |  | [Soporte para el PCB OpenCR x 4](https://github.com/amitjans/Eva3D_2.0/blob/master/stl/v4/Piezas%20generales/PCB-Support.stl) |
| <span id="Imp#15">Imp#15</span> || Soporte para el PCB ArbotiX-M x 4 |

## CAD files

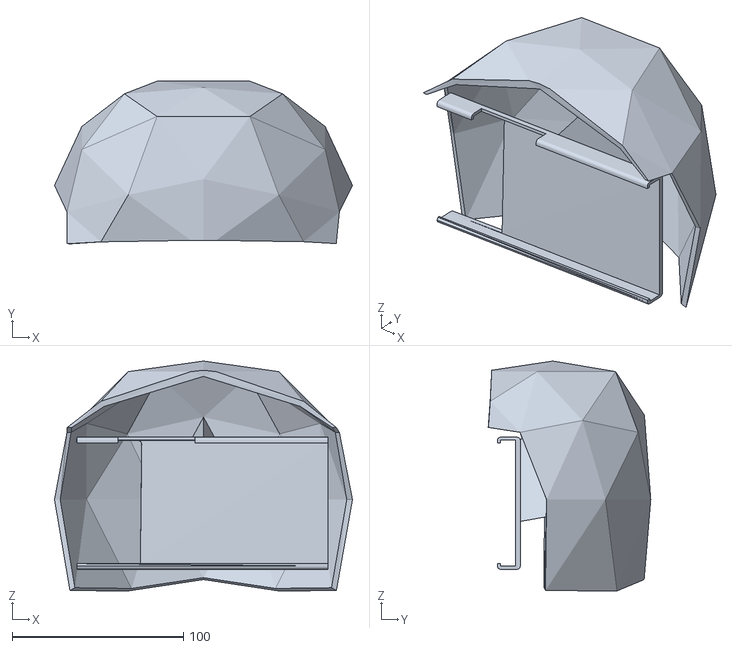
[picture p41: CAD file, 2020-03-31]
stl/eva_cabeza_2.stl
174.0 x 94.9 x 134.2

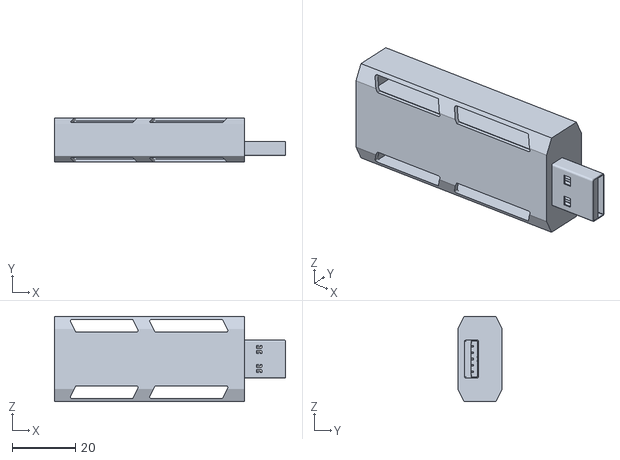
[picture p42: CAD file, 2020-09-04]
stl/externos/Intel/Intel Movidius Neural Compute Stick 2.stl
73.0 x 14.0 x 27.0

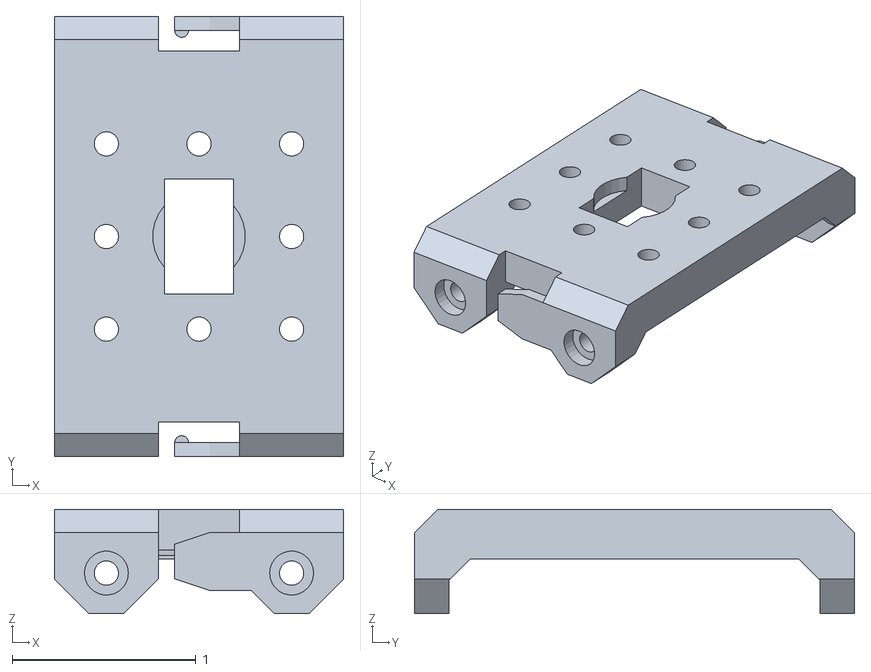
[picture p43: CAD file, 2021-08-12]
stl/externos/Motores/F3.stl
1.57 x 2.39 x 0.567

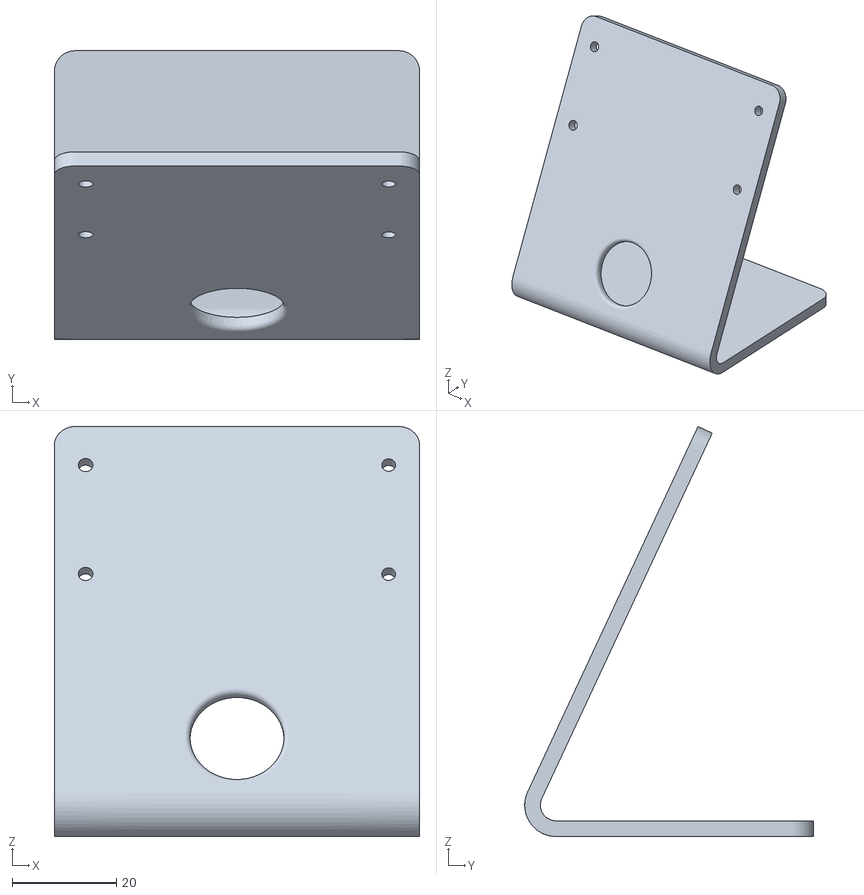
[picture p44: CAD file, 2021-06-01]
stl/externos/Raspberry Pi/Pi_Zero_Stand.stl
70.0 x 55.3 x 78.5

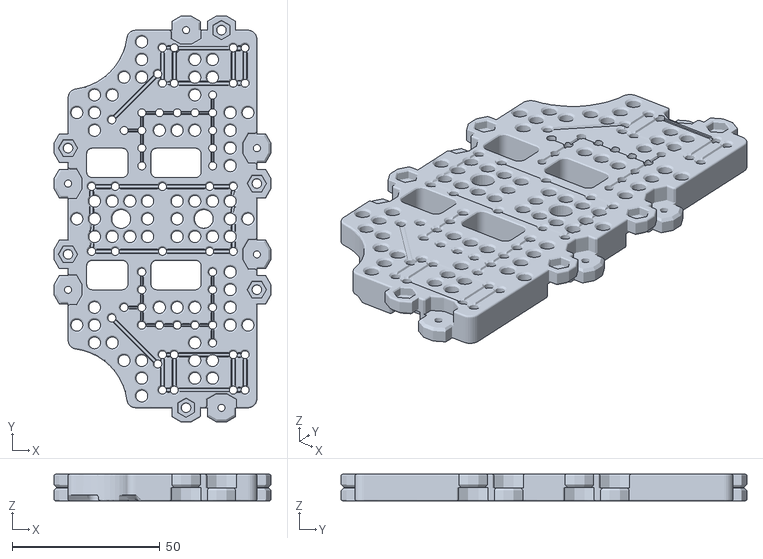
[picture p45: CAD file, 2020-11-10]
stl/externos/Turtlebot 3/Waffle-Plate.stl
73.5 x 137.5 x 9.00

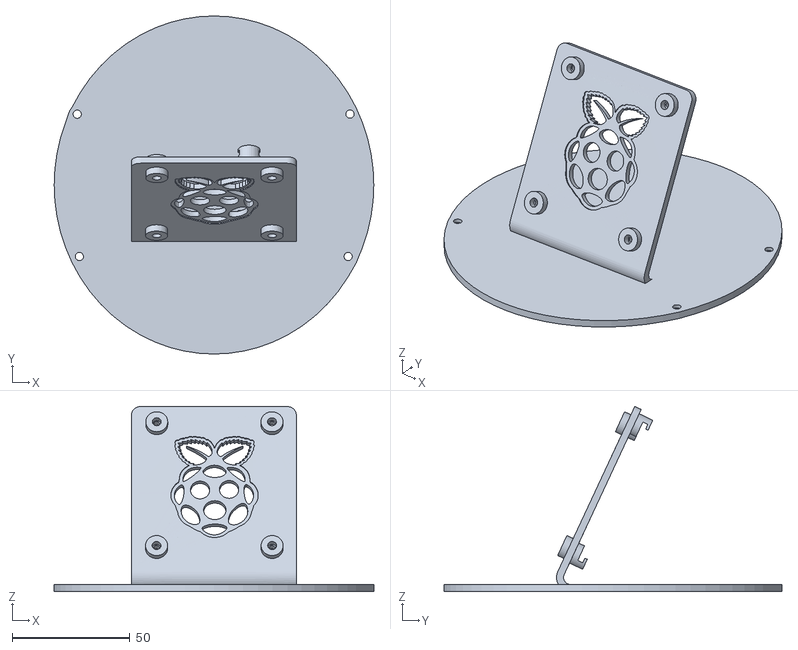
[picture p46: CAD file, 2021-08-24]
stl/Mini/Base2.stl
135.6 x 143.4 x 78.5

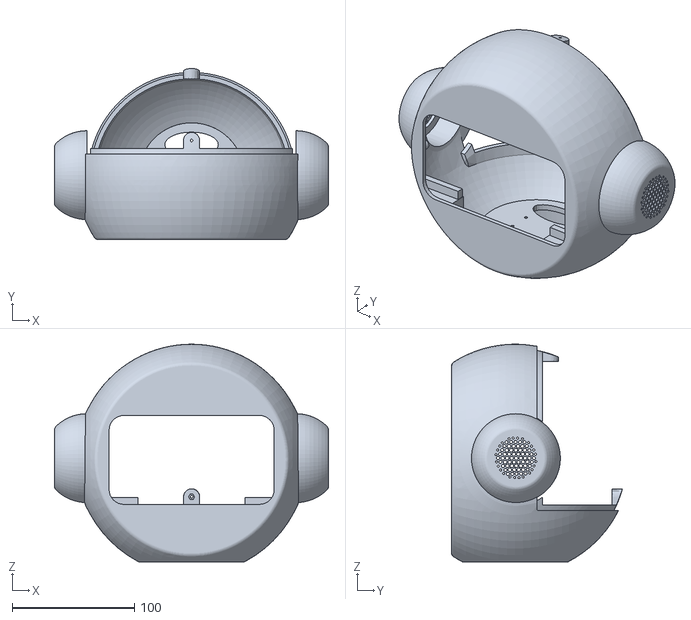
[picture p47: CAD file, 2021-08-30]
stl/v4/Basic Version/Head.stl
223.7 x 139.6 x 177.7

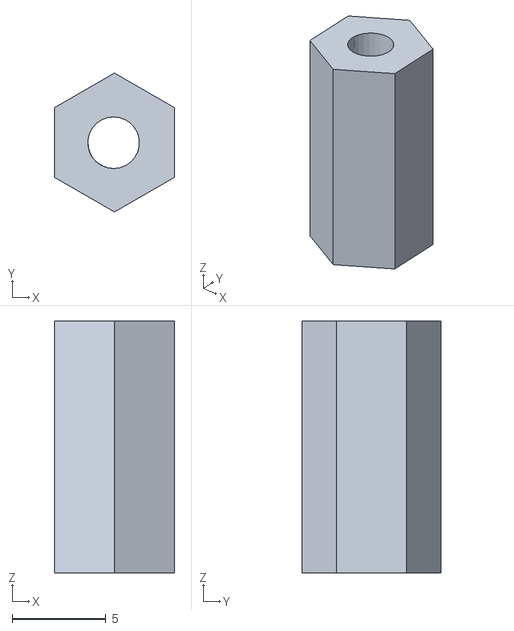
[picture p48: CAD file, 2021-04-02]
stl/v4/Common Parts (Basic and with Camera versions)/ArbotiX-M_Support.stl
6.40 x 7.39 x 13.4

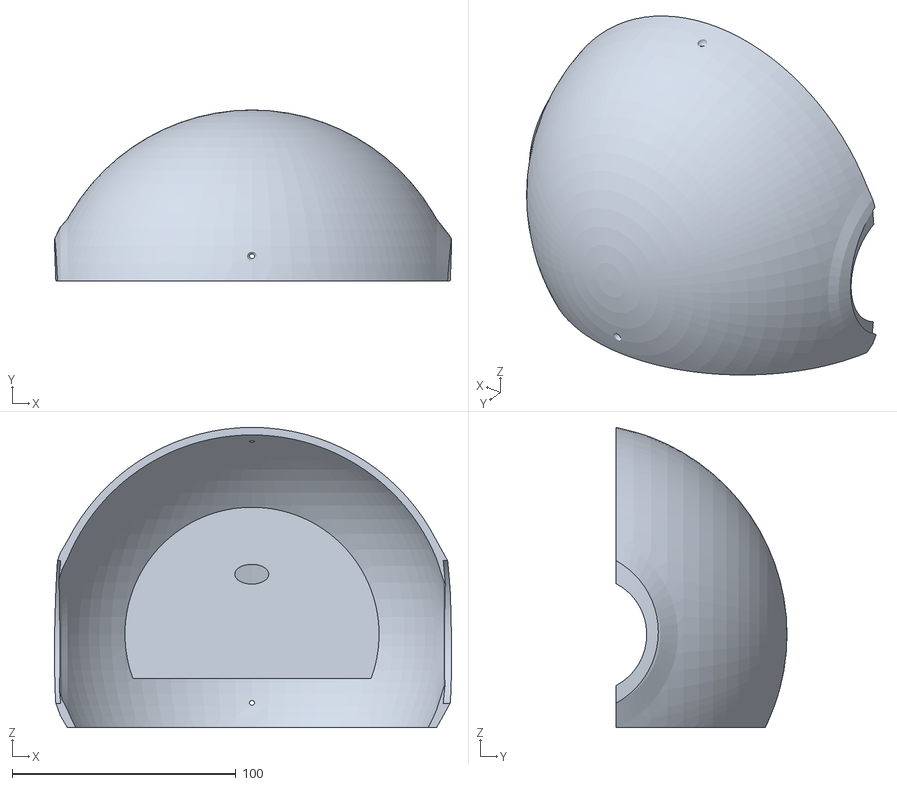
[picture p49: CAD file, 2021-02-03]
stl/v4/Common Parts/Head cover.stl
177.3 x 76.4 x 134.1

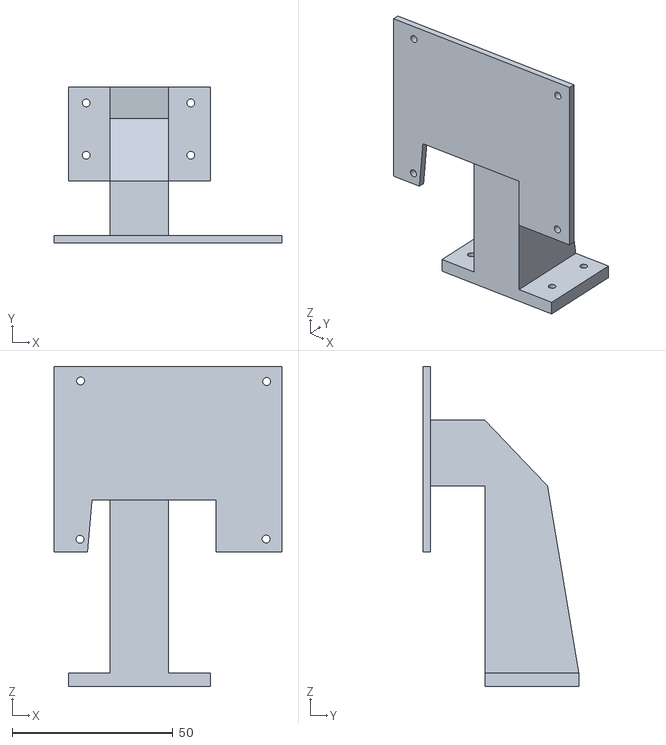
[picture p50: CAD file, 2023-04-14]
stl/v4/Screen Support (No Head).stl
70.8 x 48.4 x 99.5

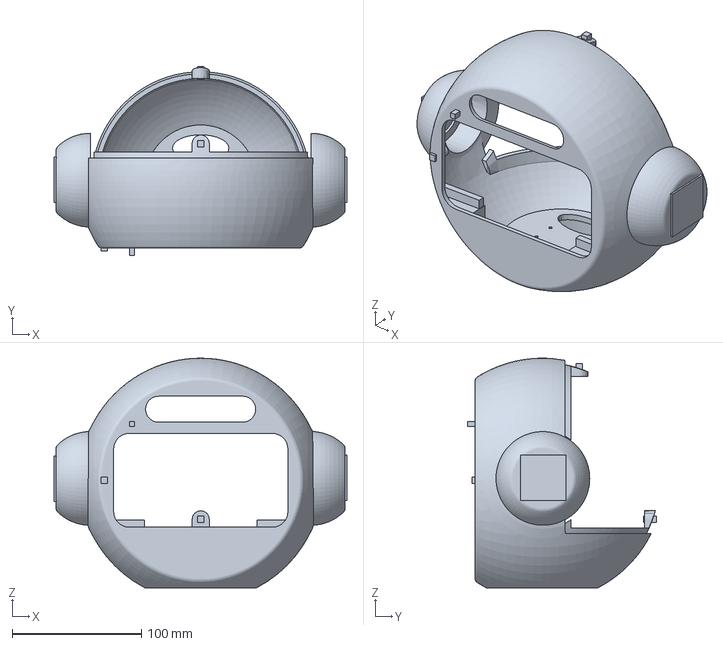
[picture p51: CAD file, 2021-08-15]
stl/v4/Version with Camera/Head_with_camera.3mf
226.7 x 146.5 x 177.7 mm

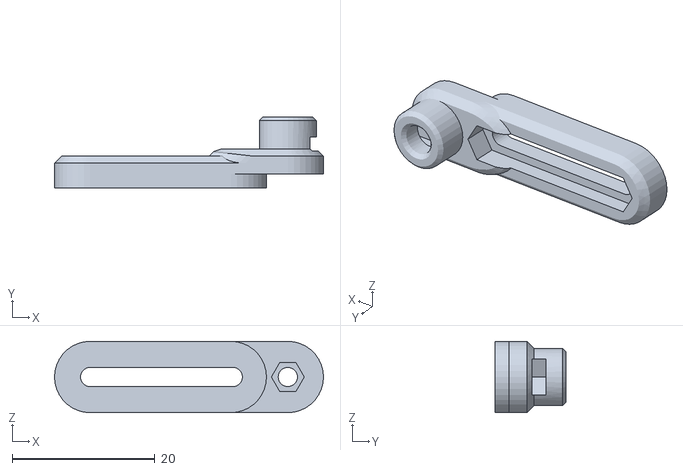
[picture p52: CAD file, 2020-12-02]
stl/v4/Version with Mobility/OpenCR-Support.stl
37.7 x 10.0 x 10.0

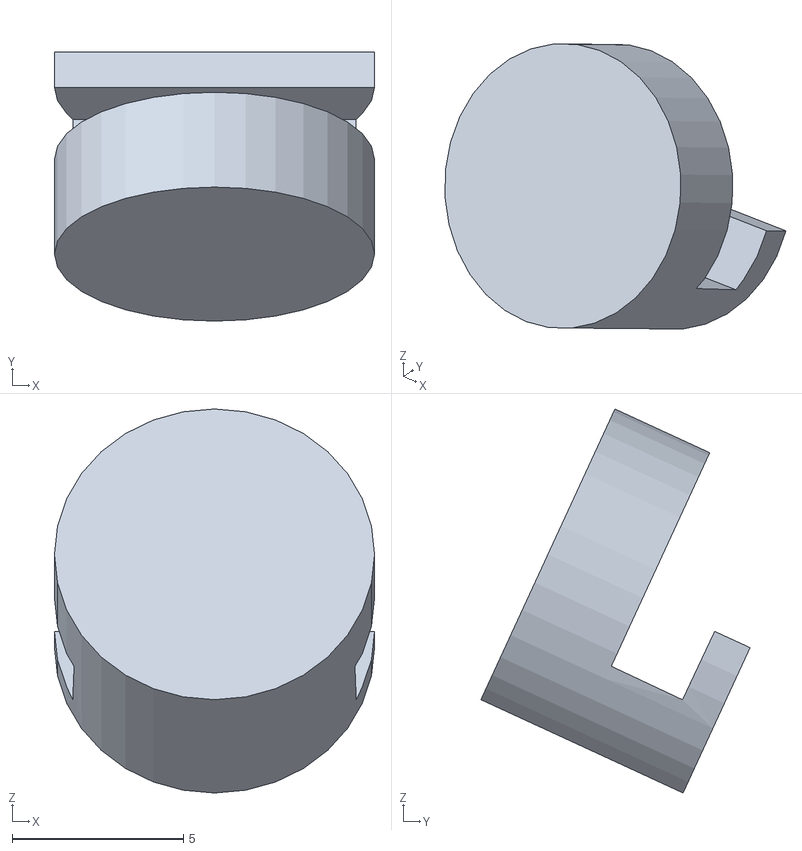
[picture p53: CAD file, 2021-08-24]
Test/MM_Test.stl
9.35 x 7.87 x 11.2

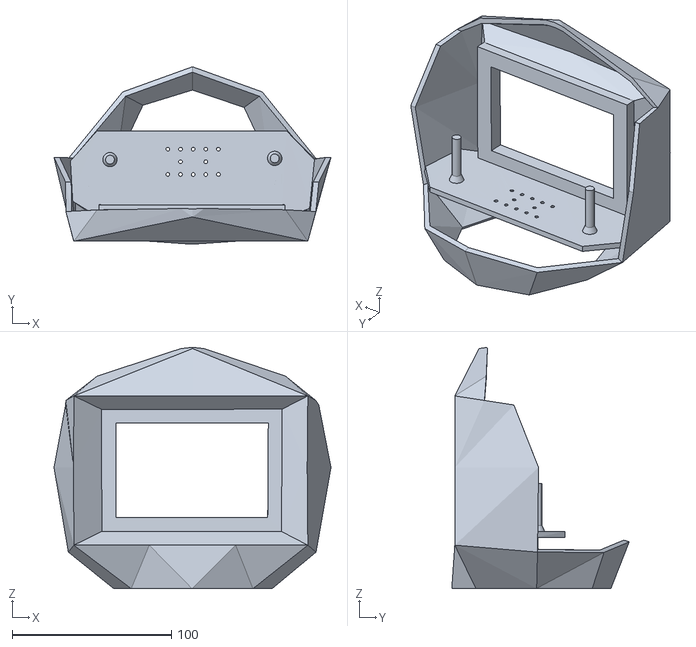
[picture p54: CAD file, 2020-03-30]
stl/eva_cabeza_1.stl
174.0 x 111.5 x 151.6

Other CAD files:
stl/externos/Motores/F2.stl
stl/externos/Raspberry Pi/Raspberry Pi 4.stl
stl/externos/Turtlebot 3/PCB_Support.stl
stl/Mini/arm.stl
Bibliotecas/Bracket.blend
Bibliotecas/PCB-Support - Long.blend
Bibliotecas/PCB-Support.blend
Bibliotecas/Plate-support.blend
Bibliotecas/Waffle-Plate.blend
Partes/Rejillas/Rejilla2.blend
Partes/Rejillas/Rejilla_orejas.blend
Test/3D_Printer_test_fixed_stl_3rd_gen.STL
Test/M1.stl
Test/M3.stl
Test/Printer Test 2.blend
Test/Printer Test 2.stl
Test/Printer Test.blend
Test/Printer Test.stl
Test/Prueba de cierre.stl
Test/Prueba de cierre2.stl
Test/Prueba de cierre3.stl
stl/Mini/Base.stl
stl/Mini/Head_cover.stl
stl/Mini/Screen_support.stl
stl/Mini/arm.joint.stl
stl/base_matrix_fibra.stl
stl/eva_base.stl
stl/eva_base_fibra.stl
stl/eva_cuerpo.stl
stl/externos/M1.stl
stl/externos/M3.stl
stl/externos/Raspberry Pi/Bottom_Hex_MM2_Color1.stl
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

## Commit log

2020-02-27 Actualización de la base del celular
    [eva_cabeza_2.stl]
2020-02-27 Actualización de la cabeza
    [eva_cabeza_1.stl]
2020-03-03 Actualización de la cabeza
    Ahora existe mas espacio para el movimiento del cuello. Se mejoraron los pilares para la unión de las partes. Se aplanaron las caras donde chocan las dos partes, para un mejor ajuste.
    [eva_cabeza_1.stl]
2020-03-03 Agregados los modelos del Case
    Se agregaron los modelos del case para el Raspberry Pi 4.
    [Bottom_Hex_MM2_Color1.stl, Top_Hex_MM2_Color1_Pins.stl]
2020-03-05 Agregada la tapa del microfono
    Se agregó la tapa del microfono a los archivos stl para imprimir.
    [star.stl]
2020-03-09 Actualizacion de fichero stl
    Actualizacion de la parte 2 de la cabeza en el fichero stl.
    [eva_cabeza_2.stl]
2020-03-20 Base para cuerpo de Fibra
    [eva_base_fibra.stl]
2020-03-24 Fibra de vidrio
    Agregado el interior para el modelo en fibra de vidrio y la base para el matrix voice de este mismo modelo.
    [base_matrix_fibra.stl]
2020-03-28 Actualización del Cuerpo
    Se niveló el cuello.
    [eva_cuerpo.stl]
2020-03-30 Error de Impresión
    Se corrigió el error de impresión en el archivo stl de la cabeza 1.
    [eva_cabeza_1.stl]
2020-03-31 Actualización Cabeza 2
    Se eliminaron caras sobrantes del modelo de la cabeza. Se mejoró el modelo del soporte del celular.
    [eva_cabeza_2.stl]
2020-08-25 Versión 3 de Eva
    [cabeza.stl, cabeza_celular.stl, cabeza_tapa.stl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]
2020-08-25 Correcciones en la malla del cuerpo
2020-08-26 Rehaciendo Versión 3
    [cuerpo.stl]
2020-08-30 Remove Doubles
    Se repararon los errores del modelo de la cabeza.
    [cabeza.stl, cabeza_celular.stl]
2020-09-04 Version 3/4 (1/-)
    [Ball_Caster.stl, Bottom_Hex_MM2_Color1.stl, Dynamixel(XL43)_Wheel_Tired_der.stl.stl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]
2020-09-04 Version 3/4 (2/-)
    [Raspberry Pi 4.stl]
2020-09-14 Modificaciones varias
    [cabeza.stl]
2020-09-14 Cambios en la cabeza
    [cabeza.stl]
2020-09-19 Cambios en el interior
    [Bateria_de_Litio.stl]
2020-09-22 Mejoras en el interior
    Se redistribuyó el interior para dar espacio a la barería
2020-09-27 Actualizacion de los stl
2020-10-01 Agregado la jetson nano
2020-10-05 Cambios varios
    [brazo.stl, cuerpo.stl, cuerpo_rejilla.stl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]
2020-10-08 Cambios interior
    [cabeza.stl, cabeza_parte.blend, cabeza_prueba.stl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]
2020-10-12 Interior
    Ajuste de la base
    [interior.stl]
2020-10-15 Ajuste soporte de pantalla
    [sopore_pantalla.stl]
2020-10-15 Cambios menores
    [baseraspberry.blend, baseraspberry.stl, interior.3mf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]
2020-10-16 Varios cambios en cabeza
    [cabeza.stl, cabeza_parte.blend, cabeza_prueba.stl]
2020-10-16 Cambios en brazos
    [brazo.stl, union_brazo.stl]
2020-11-06 Inicio de cambios del interior y rejilla
    [Turtlebot 3 - base.stl, baseraspberry.blend, cabeza_parte.blend]
2020-11-10 Variante del interior basada en Burger
    [Ball_Caster.stl, Bracket.stl, PCB_Support.stl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]
2020-11-10 Cambios interior basado en burger
    [PCB-Support.blend, Plate-support.blend, Waffle-Plate.blend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]
2020-11-16 Rejillas separadas
    [Rejilla2.blend]
2020-11-17 Cambios en base
    [Bracket.blend, base_movil.stl]
2020-11-18 Cambios en la base interna
    [base_movil_1.stl, base_movil_2.stl, soportes.stl]
2020-11-20 Cambios en el cuerpo sin pies
    [cuerpo_sinpies.stl]
2020-11-20 Correccion de la rejilla
2020-11-20 Cambios base movil
    [base_movil_1.stl, base_movil_2.stl]
2020-11-24 Ultimos cambios
    [soportes.stl]
2021-02-01 Cambio de nombre
    [soporte_pantalla.stl]
2021-02-01 Base estática
    [base.stl]
2021-02-01 Cabeza y base basicos
    [base.stl, cabeza.stl]
2021-02-03 Correcciones menores
    [cabeza_tapa.stl, tapa_cabeza.stl]
2021-04-01 Soporte para Arbotix-M
    [PCB_Support.stl]
2021-04-02 Reorganizando los archivos
    [ArbotiX-M_Support.stl, Arm joint.stl, Arm.stl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]
2021-06-01 Mini Update
    [Pi_Zero_Stand.stl]
2021-06-17 Update Mini
    [Base.stl, Head_cover.stl, Screen_support.stl]
2021-07-30 Head Update
    [pantalla.stl]
2021-08-03 Create Head with camera.gcode
2021-08-05 Head Print Mods
    [Head with camera.stl, Head_with_camera.3mf]
2021-08-12 Update Head and Nuts
    [Printer Test 2.blend, Printer Test 2.stl]
2021-08-13 Test Update
    [Printer Test 2.blend, Printer Test 2.stl]
2021-08-15 Head + Nuts
    [M1.stl, M3.stl, Printer Test 2.blend]
2021-08-15 Some Updates
    [Camera_support.stl, Head with camera.stl, M1.stl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]
2021-08-15 Update Head and Mini Model
    [Head with camera.stl, Head_with_camera.3mf, Prueba de cierre3.stl]
2021-08-24 Mini Base Update
    [Base2.stl, MM_Test.stl]
2021-08-30 Basic Head
    [Head.stl]
2022-01-14 Screen support (no head)
    [Screen Support (No Head).stl]
2023-03-22 Update mini.blend
    Pruebas con los insertos roscados
2023-04-14 feat: Nuevos modelos y cambios menores
    [Screen Support (No Head).stl]
2023-04-14 docs: :construction: Documentación de ensamblado
2023-04-14 docs: 🚧 Actualización de la documentación
